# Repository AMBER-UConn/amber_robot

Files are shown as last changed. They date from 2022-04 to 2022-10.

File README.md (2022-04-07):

# The UConn AMBER (Adaptive Morphing and Balanced Exploratory Rover) Project

A group of students at the University of Connecticut were selected as finalists in the annual NASA Big Idea Challenge ([see our submission](https://bigidea.nianet.org/wp-content/uploads/2022-BIG-Idea-Challenge-Finalist-Team-Synopses.pdf) or the [video](https://youtu.be/4zF1PQumCn8))

# Project Setup
1. Download Git - [Linux](https://git-scm.com/download/linux), [macOS](https://git-scm.com/download/mac), [Windows](https://git-scm.com/download/win)
2. Download and Setup Docker
   - [macOS](https://docs.docker.com/desktop/mac/install/) - Install Docker Desktop
   - [Windows](https://docs.docker.com/desktop/windows/install/) - Install Docker Desktop
   - [Linux](https://docs.docker.com/engine/install/)
 #### On the terminal or command prompt do the following:
3. Navigate to a directory where you want the project to be stored.
4. Clone the GitHub Repository using the command - 
```
git clone https://github.com/AMBER-UConn/amber_robot
```
5. The docker configuration files lie in the docker folder of the amber_robot project. Anytime you need to access these files to run a command, change your current directory to the docker directory.
6. Before creating and starting any docker services, you must start Docker Daemon. In Windows or macOS, you can manually do it by starting the Docker Desktop app. The state should transition to "Running" after a few seconds. In Linux you can do it [manually](https://docs.docker.com/config/daemon/systemd/) or [automatically](https://docs.docker.com/engine/install/linux-postinstall/).
7. Return to the terminal and use the command below to create and start services.
```
docker-compose --profile no-gui up
``` 

8. After a while of downloading and compiling your containers will be up and running. You should see messages sent across ROS Services:
   
```
ros_listener  | data: "yoooooooooooooooooooooooooo 1"
ros_listener  | ---
ros_listener  | data: "yoooooooooooooooooooooooooo 2"
ros_listener  | ---
ros_listener  | data: "yoooooooooooooooooooooooooo 3"
ros_listener  | ---
```

   ## Congratulations! Set up complete!
\
   Note: To stop a running container, it would be preferable if the process could shutdown smoothly instead of abruptly disconnecting users and corrupting files. Press ctrl+c and wait 10-12 seconds for the containers to stop.

   Note: To restart the containers use the command `docker-compose up`.
   
\
To open a bash terminal (Linux terminal) in the rust_ros container, start the containers using the command `docker-compose up` in one tab of the terminal, and in another tab, start a bash terminal using the command:
 ```
 docker exec -it rust_ros bash
 ```

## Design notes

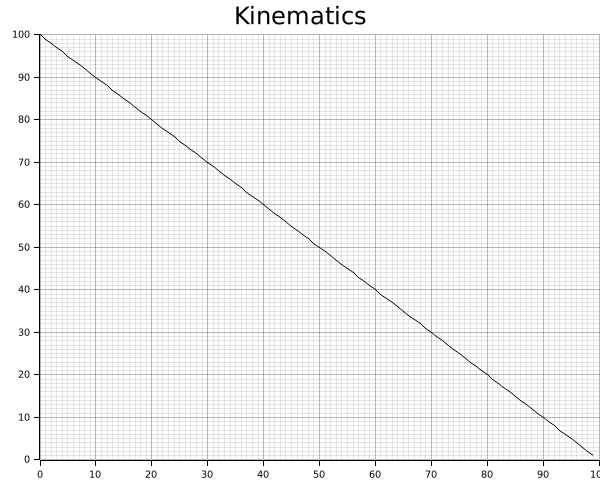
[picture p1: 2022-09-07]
rust-client/kinematics/curve.png

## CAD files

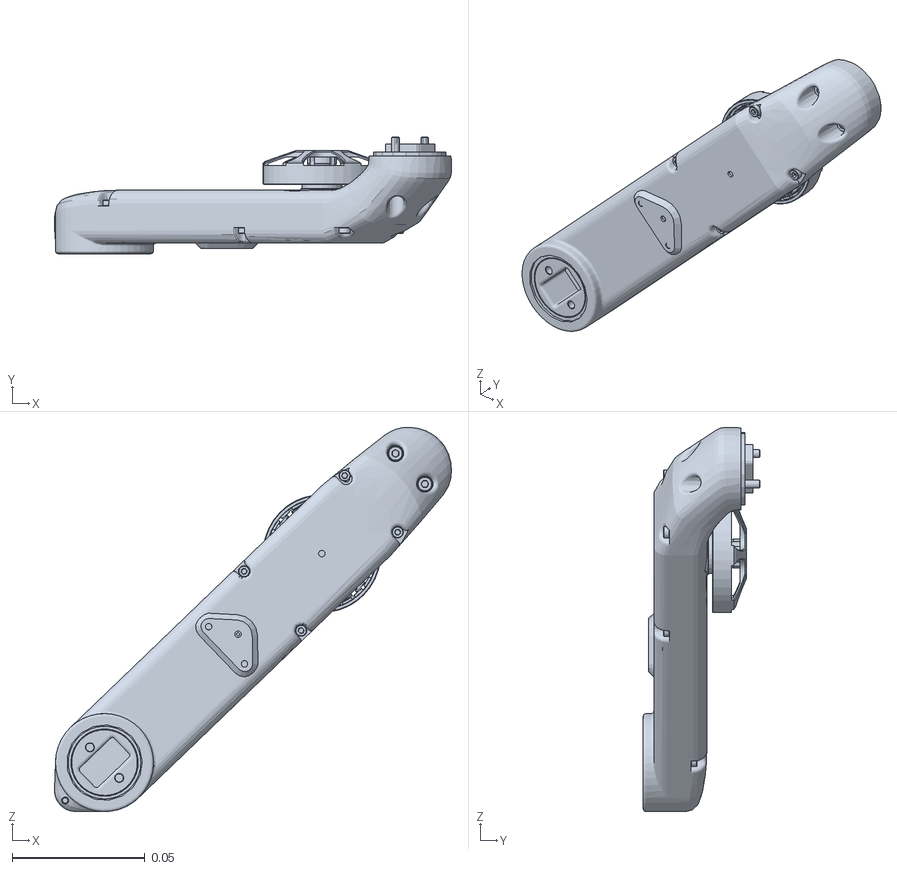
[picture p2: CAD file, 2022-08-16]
cw/src/2dof_leg_module_v3/meshes/upper_leg.STL
0.15 x 0.044 x 0.145

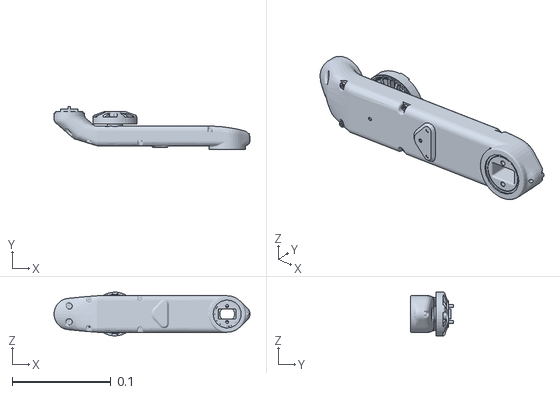
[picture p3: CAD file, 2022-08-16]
cw/src/2dof_leg_module_v3/meshes/hip_module.STL
0.199 x 0.044 x 0.0444

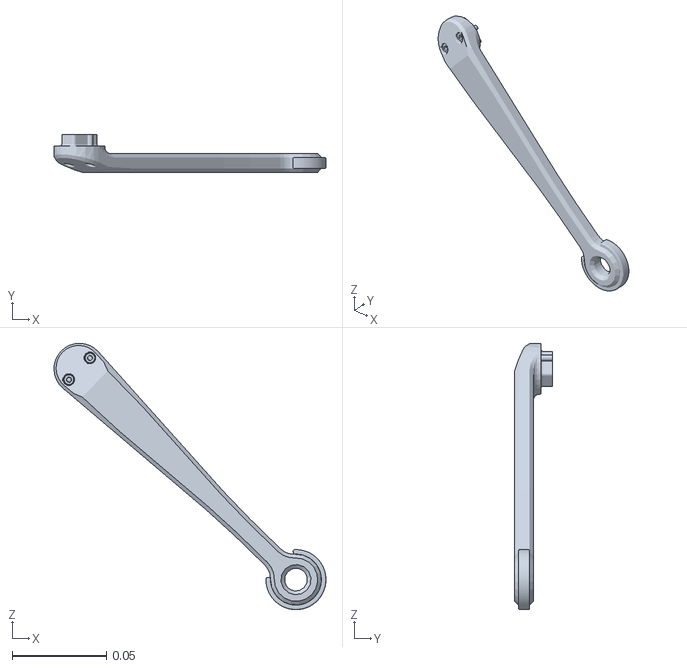
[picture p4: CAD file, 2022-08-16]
cw/src/2dof_leg_module_v3/meshes/lower_leg.STL
0.144 x 0.02 x 0.141

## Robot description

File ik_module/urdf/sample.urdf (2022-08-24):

<robot name="robo">
    <mujoco>
        <compiler meshdir="../meshes/" balanceinertia="true" discardvisual="false"/>
      </mujoco>
    <!-- links -->
    <link name="root_body">
      <inertial>
        <origin xyz="0 0 0.5" rpy="0 0 0"/>
        <mass value="1"/>
        <inertia ixx="100" ixy="0" ixz="0" iyy="100" iyz="0" izz="100" />
      </inertial>
      <visual>
        <origin xyz="0.0 0.0 0.0" rpy="0.0 0.0 0.0" />
        <geometry>
          <box size="0.2 0.2 0.4" />
        </geometry>
        <material name="Cyan">
          <color rgba="1.0 1.0 1.0 1.0"/>
        </material>
      </visual>
      <collision>
        <origin xyz="0 0 0" rpy="0 0 0"/>
        <geometry>
          <cylinder radius="1" length="0.5"/>
        </geometry>
      </collision>
    </link>
  
    <!-- left arm -->
    <link name="l_shoulder1">
      <visual>
        <origin xyz="0.0 0.0 0.0" rpy="0.0 0.0 0.0" />
        <geometry>
          <box size="0.1 0.1 0.1" />
        </geometry>
        <material name="Cyan">
          <color rgba="0 1.0 1.0 1.0"/>
        </material>
      </visual>
    </link>
    <link name="l_shoulder2">
      <visual>
        <origin xyz="0.0 0.0 0.0" rpy="0.0 0.0 0.0" />
        <geometry>
          <box size="0.1 0.1 0.1" />
        </geometry>
        <material name="Cyan">
          <color rgba="1.0 1.0 0.0 1.0"/>
        </material>
      </visual>
    </link>
    <link name="l_shoulder3">
      <visual>
        <origin xyz="0.0 0.0 0.0" rpy="0.0 0.0 0.0" />
        <geometry>
          <box size="0.1 0.1 0.2" />
        </geometry>
        <material name="Cyan">
          <color rgba="0.5 0.5 0.2 1.0"/>
        </material>
      </visual>
    </link>
    <link name="l_elbow1">
      <visual>
        <origin xyz="0.0 0.0 0.0" rpy="0.0 0.0 0.0" />
        <geometry>
          <box size="0.1 0.1 0.2" />
        </geometry>
        <material name="Cyan">
          <color rgba="0.8 0.2 0.2 1.0"/>
        </material>
      </visual>
    </link>
    <link name="l_wrist1">
      <visual>
        <origin xyz="0.0 0.0 0.0" rpy="0.0 0.0 0.0" />
        <geometry>
          <box size="0.1 0.15 0.1" />
        </geometry>
        <material name="Cyan">
          <color rgba="1.0 0.0 0.0 1.0"/>
        </material>
      </visual>
    </link>
    <link name="l_wrist2">
      <visual>
        <origin xyz="0.0 0.0 0.0" rpy="0.0 0.0 0.0" />
        <geometry>
          <box size="0.05 0.08 0.15" />
        </geometry>
        <material name="Cyan">
          <color rgba="0.0 0.0 1.0 1.0"/>
        </material>
      </visual>
    </link>
  
    <!-- right arm -->
    <link name="r_shoulder1">
      <visual>
        <origin xyz="0.0 0.0 0.0" rpy="0.0 0.0 0.0" />
        <geometry>
          <box size="0.1 0.1 0.1" />
        </geometry>
        <material name="Cyan">
          <color rgba="0 1.0 1.0 1.0"/>
        </material>
      </visual>
    </link>
    <link name="r_shoulder2">
      <visual>
        <origin xyz="0.0 0.0 0.0" rpy="0.0 0.0 0.0" />
        <geometry>
          <box size="0.1 0.1 0.1" />
        </geometry>
        <material name="Cyan">
          <color rgba="1.0 1.0 0.0 1.0"/>
        </material>
      </visual>
    </link>
    <link name="r_shoulder3">
      <visual>
        <origin xyz="0.0 0.0 0.0" rpy="0.0 0.0 0.0" />
        <geometry>
          <box size="0.1 0.1 0.2" />
        </geometry>
        <material name="Cyan">
          <color rgba="0.5 0.5 0.2 1.0"/>
        </material>
      </visual>
    </link>
    <link name="r_elbow1">
      <visual>
        <origin xyz="0.0 0.0 0.0" rpy="0.0 0.0 0.0" />
        <geometry>
          <box size="0.1 0.1 0.2" />
        </geometry>
        <material name="Cyan">
          <color rgba="0.8 0.2 0.2 1.0"/>
        </material>
      </visual>
    </link>
    <link name="r_wrist1">
      <visual>
        <origin xyz="0.0 0.0 0.0" rpy="0.0 0.0 0.0" />
        <geometry>
          <box size="0.1 0.15 0.1" />
        </geometry>
        <material name="Cyan">
          <color rgba="1.0 0.0 0.0 1.0"/>
        </material>
      </visual>
    </link>
    <link name="r_wrist2">
      <visual>
        <origin xyz="0.0 0.0 0.0" rpy="0.0 0.0 0.0" />
        <geometry>
          <box size="0.05 0.08 0.15" />
        </geometry>
        <material name="Cyan">
          <color rgba="0.0 0.0 1.0 1.0"/>
        </material>
      </visual>
    </link>
  
  

    <joint name="l_shoulder_yaw" type="revolute">
      <origin xyz="0.0 0.2 0.2" />
      <parent link="root" />
      <child link="l_shoulder1" />
      <axis xyz="0 0 1" />
      <limit lower="-3" upper="3.0" effort="0" velocity="1.0"/>
    </joint>
    <joint name="l_shoulder_pitch" type="revolute">
      <origin xyz="0.0 0.1 0.0" />
      <parent link="l_shoulder1" />
      <child link="l_shoulder2" />
      <axis xyz="0 1 0" />
      <limit lower="-3" upper="3.0" effort="0" velocity="1.0"/>
    </joint>
    <joint name="l_shoulder_roll" type="revolute">
      <origin xyz="0.0 0.1 0.0" />
      <parent link="l_shoulder2" />
      <child link="l_shoulder3" />
      <axis xyz="1 0 0" />
      <limit lower="-2" upper="3.0" effort="0" velocity="1.0"/>
    </joint>
    <joint name="l_elbow_pitch" type="revolute">
      <origin xyz="0.0 0.0 -0.2" />
      <parent link="l_shoulder3" />
      <child link="l_elbow1" />
      <axis xyz="0 1 0" />
      <limit lower="-2" upper="3.0" effort="0" velocity="1.0"/>
    </joint>
    <joint name="l_wrist_yaw" type="revolute">
      <origin xyz="0.0 0.0 -0.2" />
      <parent link="l_elbow1" />
      <child link="l_wrist1" />
      <axis xyz="0 0 1" />
      <limit lower="-2" upper="3.0" effort="0" velocity="1.0"/>
    </joint>
    <joint name="l_wrist_pitch" type="revolute">
      <origin xyz="0.0 0.0 -0.2" />
      <parent link="l_wrist1" />
      <child link="l_wrist2" />
      <axis xyz="0 1 0" />
      <limit lower="-2" upper="3.0" effort="0" velocity="1.0"/>
    </joint>
  
    <!-- right arm -->
    <joint name="r_shoulder_yaw" type="revolute">
      <origin xyz="0.0 -0.2 0.2" />
      <parent link="root" />
      <child link="r_shoulder1" />
      <axis xyz="0 0 1" />
      <limit lower="-3" upper="3.0" effort="0" velocity="1.0"/>
    </joint>
    <joint name="r_shoulder_pitch" type="revolute">
      <origin xyz="0.0 -0.1 0.0" />
      <parent link="r_shoulder1" />
      <child link="r_shoulder2" />
      <axis xyz="0 1 0" />
      <limit lower="-3" upper="3.0" effort="0" velocity="1.0"/>
    </joint>
    <joint name="r_shoulder_roll" type="revolute">
      <origin xyz="0.0 -0.1 0.0" />
      <parent link="r_shoulder2" />
      <child link="r_shoulder3" />
      <axis xyz="1 0 0" />
      <limit lower="-2" upper="3.0" effort="0" velocity="1.0"/>
    </joint>
    <joint name="r_elbow_pitch" type="revolute">
      <origin xyz="0.0 0.0 -0.2" />
      <parent link="r_shoulder3" />
      <child link="r_elbow1" />
      <axis xyz="0 1 0" />
      <limit lower="-2" upper="3.0" effort="0" velocity="1.0"/>
    </joint>
    <joint name="r_wrist_yaw" type="revolute">
      <origin xyz="0.0 0.0 -0.2" />
      <parent link="r_elbow1" />
      <child link="r_wrist1" />
      <axis xyz="0 0 1" />
      <limit lower="-2" upper="1.0" effort="0" velocity="1.0"/>
    </joint>
    <joint name="r_wrist_pitch" type="revolute">
      <origin xyz="0.0 0.0 -0.2" />
      <parent link="r_wrist1" />
      <child link="r_wrist2" />
      <axis xyz="0 1 0" />
      <limit lower="-2" upper="3.0" effort="0" velocity="1.0"/>
    </joint>
  </robot>

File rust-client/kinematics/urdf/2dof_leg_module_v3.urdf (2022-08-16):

<?xml version="1.0" encoding="utf-8"?>
<!-- This URDF was automatically created by SolidWorks to URDF Exporter! Originally created by Stephen Brawner (brawner@gmail.com) 
     Commit Version: 1.6.0-4-g7f85cfe  Build Version: 1.6.7995.38578
     For more information, please see http://wiki.ros.org/sw_urdf_exporter -->
<robot name="2dof_leg_module_v3">
  <mujoco>
    <compiler meshdir="../meshes/" balanceinertia="true" discardvisual="false"/>
  </mujoco>
  <link name="hip_module">
    <inertial>
      <origin xyz="-0.0135872417794477 0.00419665468565325 -0.0185249720276986" rpy="0 0 0" />
      <mass value="0.0938334172894058" />
      <inertia ixx="1.46634528569586E-05" ixy="1.02326144382057E-05" ixz="-7.7018336582582E-08" iyy="0.000157483495316331" iyz="6.78740712115125E-09" izz="0.000152202454585631" />
    </inertial>
    <visual>
      <origin xyz="0 0 0" rpy="0 0 0" />
      <geometry>
        <mesh filename="package://2dof_leg_module_v3/meshes/hip_module.STL" />
      </geometry>
      <material name="">
        <color rgba="0.752941176470588 0.752941176470588 0.752941176470588 1" />
      </material>
    </visual>
    <collision>
      <origin xyz="0 0 0" rpy="0 0 0" />
      <geometry>
        <mesh filename="package://2dof_leg_module_v3/meshes/hip_module.STL" />
      </geometry>
    </collision>
  </link>
  <link name="upper_leg">
    <inertial>
      <origin xyz="-0.0578208195636141 -0.0212739250328726 -0.0555577921645933" rpy="0 0 0" />
      <mass value="0.094277083667373" />
      <inertia ixx="8.19279303589027E-05" ixy="-7.26529131974399E-06" ixz="-6.98506331572851E-05" iyy="0.000159785167856354" iyz="-6.99467251943385E-06" izz="8.72625226077833E-05" />
    </inertial>
    <visual>
      <origin xyz="0 0 0" rpy="0 0 0" />
      <geometry>
        <mesh filename="package://2dof_leg_module_v3/meshes/upper_leg.STL" />
      </geometry>
      <material name="">
        <color rgba="0.752941176470588 0.752941176470588 0.752941176470588 1" />
      </material>
    </visual>
    <collision>
      <origin xyz="0 0 0" rpy="0 0 0" />
      <geometry>
        <mesh filename="package://2dof_leg_module_v3/meshes/upper_leg.STL" />
      </geometry>
    </collision>
  </link>
  <joint name="hip_joint" type="continuous">
    <origin xyz="0.066577 -0.011968 -0.0185" rpy="0 0 0" />
    <parent link="hip_module" />
    <child link="upper_leg" />
    <axis xyz="0 1 0" />
  </joint>
  <link name="lower_leg">
    <inertial>
      <origin xyz="0.047875486284217 -0.0138955733287597 -0.0466193127886608" rpy="0 0 0" />
      <mass value="0.0374009758334682" />
      <inertia ixx="5.04189375716838E-05" ixy="1.3994879750165E-06" ixz="4.99489822029058E-05" iyy="0.000102550238222013" iyz="-1.36276953731254E-06" izz="5.30753304664563E-05" />
    </inertial>
    <visual>
      <origin xyz="0 0 0" rpy="0 0 0" />
      <geometry>
        <mesh filename="package://2dof_leg_module_v3/meshes/lower_leg.STL" />
      </geometry>
      <material name="">
        <color rgba="0.752941176470588 0.752941176470588 0.752941176470588 1" />
      </material>
    </visual>
    <collision>
      <origin xyz="0 0 0" rpy="0 0 0" />
      <geometry>
        <mesh filename="package://2dof_leg_module_v3/meshes/lower_leg.STL" />
      </geometry>
    </collision>
  </link>
  <joint name="knee_joint" type="continuous">
    <origin xyz="-0.11534 -0.0324 -0.11089" rpy="0 0 0" />
    <parent link="upper_leg" />
    <child link="lower_leg" />
    <axis xyz="0 1 0" />
  </joint>
</robot>

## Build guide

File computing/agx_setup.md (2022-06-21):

# Configuring CAN on the AGX
See [this article](https://medium.com/@ramin.nabati/enabling-can-on-nvidia-jetson-xavier-developer-kit-aaaa3c4d99c9) for a more detailed overview
1. Install `busybox` to change register values
```sudo apt install busybox```

2. The can_setup.sh script should run at the start but if not, you can run it manually

*Note* the pinout of the AGX fallows the Raspi 40 pin standard normally but the following pin configurations are changed
_Pin | Type_
37/29 | CAN RX
33/31 | CAN TX
34/30 | Ground
17/1  | 3.3V

## How to start `can_setup.sh` on startup
1. Create a symlink for the can_setup.sh script onto the root directory
`ln -s ~/amber_robot/computing/can_setup.sh /`
2. Run the enable_can_setup.sh script which should automatically configure the script to run on startup

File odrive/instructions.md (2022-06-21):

To start the odrive make sure that 
1. All the motor phase wires are plugged in
2. The power supply is plugged into an outlet
3. The odrive is connected to the AGX via USB

To start an interactive session with the odrive, run `odrivetool` in the terminal

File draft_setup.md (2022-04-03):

# General information
There are several main components interacting in this project. We will be building our design off the ROS framework () which is language agnostic (can use anything). Which is the reason why we are building our project off of Rust!

### Why Rust? ###

**A few main benefits:**
- Statically typed (unlike Python)
- Memory safety out of the box (no null pointers, dangling references)
- Thread safety out of the box
- Package management (which is non-existent with C++)

However, there are also a few pratical reasons outside the tech specs of the language. We have to face the reality that we do not know everything. We are not well versed in the intricacies of the frameworks, programming languages, and even the concepts we are trying to implement. And it may seem counter-intuitive that having everyone learn a whole new language is time efficient, but in reality we are saving ourselves from a world of pain by using Rust (over the alternative of C++). We would like to increase our chances of bowling a perfect 300, and Rust is basically the gutterball guard rail preventing us from messing up. 

I do concede that the documentation is less available for Rust based ROS projects, however there is enough to build off of for our purpose. We are going to build off of the package `rosrust` (which is just a Rust client implementation for ROS).

However I highly recommend that we take inspiration from the `openrr` on how to architecture our code since it has many many functions that we need for our purposes already implemented. Unfortunately, after some testing, not all of the code compiles so we can't build off of it directly (not to mention a lack of documentation).

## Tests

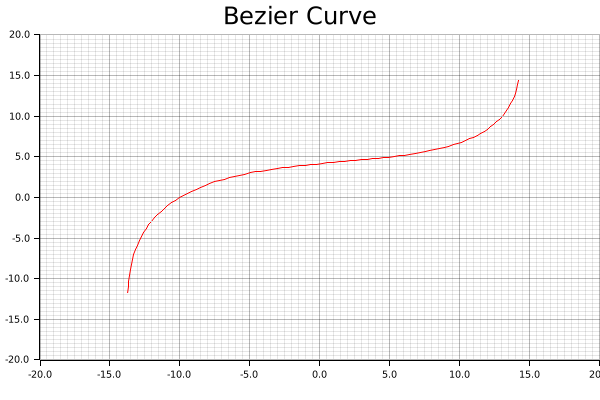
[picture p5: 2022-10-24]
rust-client/kinematics/test.png

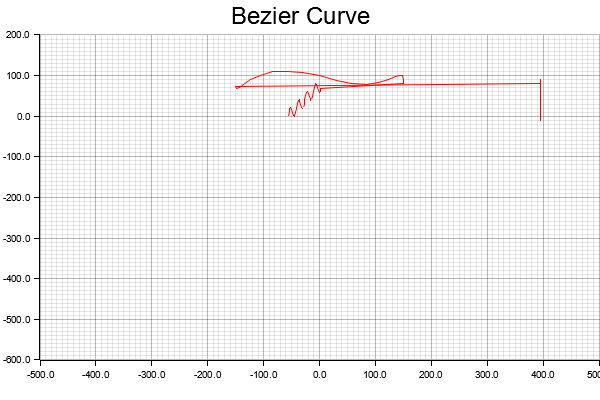
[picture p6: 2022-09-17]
rust-client/kinematics/src/test.png

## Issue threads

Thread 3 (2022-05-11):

Configure odrives with the motors, jetson, power supply, and odrives

kalinkochnev, 2022-05-11:

kalinkochnev, 2022-07-01:
Single power supply and odrive have been wired and functional for quite some time. Now we are focusing on finding the proper batteries and avoiding ground loops

Closed 2022-07-01.

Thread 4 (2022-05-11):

Create sketch (and CAD drawing) for leg test stand V1

kalinkochnev, 2022-05-11:
We need to build a leg test stand, preferably before the mid project report or have made big strides towards building one. We will have some spare wood to work with from the MSL, as well as 3D printers and the likes of that. Try to avoid building this with any parts we do not have easily accessible. Reference our stock sheet for what we have available.

**Build requirements:**
1. Have a stable foundation that can avoid shaking too much and can be clamped down
2. Be tall enough the have the leg fully extended vertically and not be touching the surface the stand is on, plus add an 2 inches of extra height so that we may be able to put things below the leg without issue.
3.  Have a place to mount an ODrive and a power supply (where the odrive and power supply should be able to be removed). _Suggestions_: 3d print mounting brackets so things can slide in and out.

4. Have cables be routed to avoid getting tangled up in the leg (also may want to 3d print cable brackets of some kind)
5. Be able to screw the leg into the beam somehow

Message Kalin to measure dimensions of parts when he's in the lab (e.g. power supply, wood beams, odrive, etc)

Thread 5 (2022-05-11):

2 DOF Leg simulation in Gazebo

kalinkochnev, 2022-05-11:
Use gazebo to simulate a fixed base, 2 degree of freedom leg.

**Requirements**
1. Make a rudimentary URDF model of a 2 DOF leg (someone else will be tasked with creating a more accurate one)
2. Control the simulated leg through the rosrust client (just needs to move somehow, could spin in circles for all I care)
3. Figure out how to actually control the simulated leg well. We are effectively building a robot arm, so I'm sure there are a lot of tutorials on how to do inverse kinematics.

**Suggestions**
- look into the ROS package called ros_control for motor control (which is pretty popular and should maybe be able to integrate with gazebo. This is what the odrive motor controller package is build off of, so it should be swappable)
- Try using the `ikfast` library http://wiki.ros.org/Industrial/Tutorials/Create_a_Fast_IK_Solution, http://openrave.org/docs/latest_stable/openravepy/ikfast/#ik-types

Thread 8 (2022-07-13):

OPAMP_DISABLED

UltraArceus3, 2022-07-13:
Seemingly at random, the motors would refuse to beep and turn during full calibration sequence. Instead, the motor would either twitch in-place or do nothing at all. This would seemingly come in and out at inconvenient times.
Checking the motor for errors would reveal a 'MotorError.OPAMP_DISABLED' error. There are no documentations nor resources from ODrive discussing the error, the cause of the error, or a solution. Asking on the ODrive forums or Discord has shown that no one knows what the error is nor the cause of it.

UltraArceus3, 2022-07-13:
Some temporary solutions I've found while testing:
- Unplugging and plugging in the ODrive
- Swapping the motors between axes / ODrives
- Tilting the motor at an angle or placing it upside-down
- Slightly bending the motor's cable
- Repeatedly sending the Full Calibration Sequence command

I have not tested these enough to know if they truly work as this error does come and go randomly, so some of these may be false positives.

UltraArceus3, 2022-07-14:
https://discourse.odriverobotics.com/t/op-amp-error-odrive/9443

UltraArceus3, 2022-07-14:
According to the forum post, OPAMP_DISABLED is an outdated error w/ its corresponding value being reassigned to UNBALANCED_PHASES.
Upon further research, UNBALANCED_PHASES may be remedied by using thicker gauge wires.

UltraArceus3, 2022-07-14:
Swapping the 26AWG motor cables with 22AWG seems to have remedied the error from all the motors.

Further testing is needed, but the issue seems to have disappeared. I'll reopen this if the error comes up again.

Closed 2022-07-14.

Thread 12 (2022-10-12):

Controlling tank tread motors via RP4

kalinkochnev, 2022-10-12:
**Task:**
make an API for CAN communication from the Arduino to the RP4 for tread motor control

**Tread control requirements:**
- Individually addressable motors
- Set parameters such as velocity, direction

**Implementation:**
- Raspberry Pi sends commands across CAN
- Rust client maintains current state of tread control, commands sent update internal state as well, returns a result
- Arduino processes incoming messages across CAN
- Arduino responds with OK message if successful, Err if not

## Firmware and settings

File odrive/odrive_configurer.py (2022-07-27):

"""This files should be run to either reset or setup an odrive that uses 2 Antigravity motors

https://store.tmotor.com/goods.php?id=438
https://docs.odriverobotics.com/v/latest/getting-started.html

Before running the script, make sure you activate `odrivetool` and then
add this python package to the list of modules at runtime 

```
import sys
sys.path.insert(1, "/home/nvidia/amber_robot/odrive") # 0 is the odrivetool script path, 1 is the place we want to put our package

import setup
setup.setup_axes(odrv0, [odrv0.axis0, odrv0.axis1])
```
"""

#from tkinter import S
from typing import List
from odrive.enums import *
import odrive
from fibre.libfibre import ObjectLostError
import time
import sys
import init_motors


class RoverMotorConfig:
    """
    Class for configuring an Odrive axis for a Amber motor. 
    Only works with one Odrive at a time.
    """
    ########
    MOTOR_KV = 300
    ENCODER_CPR = 8192  # counts per revolution for the AMT - 102 Encoder
    NUM_POLES = 24
    VBUS_VOLTAGE = 24
    CAN_BAUD_RATE = 250000


    def __init__(self, axis_num, odrv, sensorless = False, _output = True, _force_sensorless = True):
        """
        Initalizes RoverMotorConfig class by finding odrive, erase its 
        configuration, and grabbing specified axis object.

        :param axis_num: Which channel/motor on the odrive your referring to.
        :type axis_num: int (0 or 1)
        """
        self.axis_num = axis_num
        self.axis = None
        self.odrv = odrv
        self.sensorless = sensorless
        self._force_sensorless = _force_sensorless

        self.output = _output
        # Connect to Odrive

        self.axis = self.get_axis(self.axis_num, self.odrv)

    @classmethod
    def get_odrive(cls, output = False):
        # connect to Odrive
        print("Looking for ODrive...") if output else None
        odrv = odrive.find_any()
        print("Found ODrive.") if output else None
        return odrv

    @classmethod
    def get_axis(cls, axis_num, odrv):
        return getattr(odrv, f"axis{axis_num}")

    @classmethod
    def config_power_supply(cls, odrv):
        #  power configuration for AC/DC Power Supply
        odrv.config.dc_bus_overvoltage_trip_level = 25
        odrv.config.dc_max_positive_current = 10
        odrv.config.dc_max_negative_current = -1

    @classmethod
    def config_lipo_battery(cls, odrv):
        print("Please enter battery ratings as asked.")
        batt_n_cells = int(input("Enter number of cells in series: "))
        batt_capacity = int(input("Enter battery capacity in mAh: ")) / 1000
        odrv.config.dc_bus_undervoltage_trip_level = 3.25 * batt_n_cells
        odrv.config.dc_bus_overvoltage_trip_level = 4.25 * batt_n_cells
        #self.odrv.config.dc_max_positive_current = batt_capacity * 50
        #self.odrv.config.dc_max_negative_current = -batt_capacity * 1 # CHECK THIS CAREFULLY

    def configure(self, CAN_id):
        # This is to lower the amount of power going back into the odrive when the motor is braking
        self.odrv.config.enable_brake_resistor = True

        

        self.config_motors()
        self.config_sensorless() if self.sensorless else self.config_encoder()
        self.config_CAN(CAN_id)

        self.axis.controller.config.control_mode = CONTROL_MODE_VELOCITY_CONTROL
        self.axis.controller.config.vel_limit = 50

        self.odrv.config.brake_resistance = 1
        self.axis.controller.config.input_mode = INPUT_MODE_VEL_RAMP
        

        return self.odrv

    
    def config_motors(self):
        # The motors have a peak current of 9 amps
        self.axis.motor.config.current_lim = 9
        self.axis.motor.config.requested_current_range = 10

        # The speed of the motor will be limited to this speed in [turns/sec]
        self.axis.controller.config.vel_limit = 50
        self.axis.motor.config.pole_pairs = RoverMotorConfig.NUM_POLES / 2 # The MN4004 has 24 magnet poles, so 12 pole pairs
        # The MN4004 has an idle current of 0.2 A but we set it at 2 for it to go faster during calibration
        self.axis.motor.config.calibration_current = 2
        
        self.axis.config.calibration_lockin.current = 2
        # to avoid motors from heating up when finding index (ENCODER_INDEX_SEARCH)
        
        # this is specified in the odrive documentation
        self.axis.motor.config.torque_constant = 8.27 / RoverMotorConfig.MOTOR_KV
        # self.axis.motor.config.resistance_calib_max_voltage = 0.4 * VBUS_VOLTAGE ****do not use

        self.axis.motor.config.motor_type = MOTOR_TYPE_HIGH_CURRENT

    def config_encoder(self):
        if self.axis.config.enable_sensorless_mode: return

        self.axis.controller.config.vel_gain = 0.01
        self.axis.controller.config.pos_gain = 212.0

        #vel_integrator_gain = 0.5 * vel_gain * bandwidth (in hertz)
        self.axis.controller.config.vel_integrator_gain = 0.5 * self.axis.controller.config.vel_gain * 1/(self.axis.encoder.config.bandwidth/1000)

        self.axis.encoder.config.cpr = RoverMotorConfig.ENCODER_CPR
        #self.axis.encoder.config.mode = ENCODER_MODE_INCREMENTAL
        self.axis.encoder.config.use_index = True

    def config_sensorless(self):
        self.axis.config.enable_sensorless_mode = True

        self.axis.controller.config.vel_gain = 0.01
        self.axis.controller.config.vel_integrator_gain = 0.05

        # 5 turns_per_sec / (2 * 3.14159265 * NUM_POLES / 2)
        self.axis.sensorless_estimator.config.pm_flux_linkage = 5.51328895422 / (2 * RoverMotorConfig.NUM_POLES * RoverMotorConfig.MOTOR_KV)

    def config_CAN(self, can_axis_id):
        self.odrv.can.config.baud_rate = RoverMotorConfig.CAN_BAUD_RATE
        self.axis.config.can.node_id = can_axis_id

    def check_error(self, obj):
        if hasattr(obj, "error"):
            if obj.error != 0:
                print("\nERROR \n"
                      "ODrive reported error {}.\n"
                      "Dumping object data:\n{}\n".format(obj.error, obj))
                return False
        return True

    def motor_calib(self):
        print("\nCalibrating Motor {} (You should hear a beep)...".format(self.axis_num))
        self.axis.requested_state = AXIS_STATE_MOTOR_CALIBRATION

        # Wait for calibration to take place
        wait_until(lambda : self.axis.motor.config.phase_inductance != 0)
        print("phase inductance: {}".format(self.axis.motor.config.phase_inductance))

        if self.check_error(self.axis.motor):
            self.axis.motor.config.pre_calibrated = True


    def encoder_calib(self, use_index=True, sensorless_enc_error = True):
        #Skips Encoder Calibration if Motor Calibration failed
        if not(self.axis.motor.config.pre_calibrated):
            return

        if use_index:
            self.axis.encoder.config.use_index = True
            print("Rotating Encoder {} back to index...".format(self.axis_num))
            self.axis.requested_state = AXIS_STATE_ENCODER_INDEX_SEARCH
            time.sleep(3)


        print("Calibrating Encoder {} (The motor should rotate back-and-forth)...".format(self.axis_num))
        self.axis.requested_state = AXIS_STATE_ENCODER_OFFSET_CALIBRATION
        #waits until encoder finishes calibrating or throws an error
        wait_until(
            lambda :
            (abs(self.axis.encoder.config.direction) == 1 and
            self.axis.encoder.config.phase_offset != 0) or
            self.axis.encoder.error != 0
            )

        if self.check_error(self.axis.encoder):
            self.axis.encoder.config.pre_calibrated = True
        elif sensorless_enc_error:
            print("Encoder Error")
            if self._force_sensorless:
                print("Reverting to sensorless mode...")
                self.sensorless = True
                self.config_sensorless()
            #If there is an encoder error (i.e. encoder isn't detected), the motor becomes sensorless
            

    def run_calib(self, odrv):
        self.odrv = odrv
        self.axis = self.get_axis(self.axis_num, self.odrv)
        self.motor_calib()
        self.encoder_calib() if not(self.sensorless) else None

def save(odrv = RoverMotorConfig.get_odrive()):
    try:
        odrv.save_configuration()
    except ObjectLostError:
        pass
    return RoverMotorConfig.get_odrive()

def wait_until(cond, sec_limit: float = 10.0):
    tick = 0
    while not(cond()) and tick < sec_limit:
        time.sleep(0.1)
        tick += 0.1
    print("wait timed out") if tick >= sec_limit else None

def main():
    odrv = RoverMotorConfig.get_odrive(True)
    print("Erasing pre-existing configuration...")
    try:
        odrv.erase_configuration()
    except:
        pass

    odrv = RoverMotorConfig.get_odrive()

    odrv_can_id = 2 * int(input("ODrive CAN ID > "))

    odrive_config1 = RoverMotorConfig(axis_num = 0, _force_sensorless = False, odrv = odrv)
    odrv = odrive_config1.configure(CAN_id = odrv_can_id)

    odrive_config2 = RoverMotorConfig(axis_num = 1, _force_sensorless = False, odrv = odrv)
    odrv = odrive_config2.configure(CAN_id = odrv_can_id + 1)


    power_supply_type = int(input("Enter 1 for Bench Power Supply or 2 for Battery > "))
    match power_supply_type:
        case 1:
            RoverMotorConfig.config_power_supply(odrv)
        case 2:
            RoverMotorConfig.config_lipo_battery(odrv)
        case _:
            raise ValueError("Incorrect Input!")

    odrv = save(odrv)
    
    input("Make sure the motor is free to move, then press enter...")

    odrive_config1.run_calib(odrv)
    odrive_config2.run_calib(odrv)

    print("Saving...")
    odrv = save(odrv)
    print("Calibration Complete!")
    return odrv


if __name__ == "__main__":
    o = main()

    print("Initializing Motors...")
    init_motors.init(o)

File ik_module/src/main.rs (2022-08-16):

use k::*;

fn main() {
    // // Load urdf file
    // let chain = k::Chain::<f32>::from_urdf_file("/home/vihaan/Projects/amber/amber_robot/ik_module/urdf/2dof_leg_module_v3.urdf").unwrap();
    // println!("chain: {chain}");
    // assert_eq!(chain.dof(), 2);

    // // // Set initial joint angles
    // // let angles = vec![0.2, 0.2, 0.0, -1.0, 0.0, 0.0, 0.2, 0.2, 0.0, -1.0, 0.0, 0.0];
    // let angles = vec![0.0, 0.0];
    // println!("angles: {:?}", angles);


    // chain.set_joint_positions(&angles).unwrap();
    // println!("initial angles={:?}", chain.joint_positions());

    // let target_link = chain.find("hip_joint").unwrap();

    // // Get the transform of the end of the manipulator (forward kinematics)
    // chain.update_transforms();
    // let mut target = target_link.world_transform().unwrap();

    // println!("initial target pos = {}", target.translation);
    // // println!("move z: +0.1");
    // // target.translation.vector.z += 0.1;

    // // Create IK solver with default settings
    // let solver = k::JacobianIkSolver::default();

    // // Create a set of joints from end joint
    // let arm = k::SerialChain::from_end(target_link);
    // println!("arm dof {}", arm.dof());

    // // solve and move the manipulator angles
    // solver.solve(&arm, &target).unwrap();
    // println!("solved angles={:?}", chain.joint_positions());

    // chain.update_transforms();
    // let solved_pose = target_link.world_transform().unwrap();
    // println!("solved target pos = {}", solved_pose.translation);




    use k::prelude::*;

    let chain = k::Chain::<f32>::from_urdf_file("/home/vihaan/Projects/amber/amber_robot/ik_module/urdf/2dof_leg_module_v3.urdf").unwrap();
    // Create sub-`Chain` to make it easy to use inverse kinematics
    let target_joint_name = "hip_joint";
    let r_wrist = chain.find(target_joint_name).unwrap();
    let mut arm = k::SerialChain::from_end(r_wrist);
    println!("arm: {arm}");

    // Set joint positions of `arm`
    let positions = vec![0.0];
    arm.set_joint_positions(&positions).unwrap();
    println!("initial positions={:?}", arm.joint_positions());

    // Get the transform of the end of the manipulator (forward kinematics)
    let mut target = arm.update_transforms().last().unwrap().clone();

    println!("initial target pos = {}", target.translation);
    println!("move x: -0.1");
    target.translation.vector.x -= 0.1;
    
    // Create IK solver with default settings
    let solver = k::JacobianIkSolver::default();

    let mut constraints = k::Constraints::default();
    constraints.rotation_x = false;
    constraints.rotation_z = false;
    constraints.position_x = false;
    constraints.position_y = false;
    constraints.position_z = false;

    solver
        .solve_with_constraints(&arm, &target, &constraints)
        .unwrap_or_else(|err| {
            println!("Err: {err}");
   });
    // solve and move the manipulator positions
    // solver.solve(&arm, &target).unwrap();


    println!("solved positions={:?}", arm.joint_positions());
}

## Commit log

2022-03-29 Added urdf-visualizer
    [test.urdf]
2022-03-30 Added basic setup instructions
    [test.urdf]
2022-04-03 Made progress towards running rust inside container
    [test.urdf]
2022-06-09 Succesfully created odrive configuration to spin motors
2022-06-10 Added instructions to start odrive
2022-06-17 ODrive CAN control demonstrated with test script
2022-06-20 Added ODrive CAN and AxisState constants.
2022-06-20 Outlined abstracted methods for ODrive CAN calls
2022-06-21 Odrive configuration was significantly improved. Calibration sequence does not run correctly
    [streamlined_odrive_config.py]
2022-06-21 CAN data successfully received by Odrive from Rust!
2022-06-21 Outlined CANManager, ODrive message and responses. Setup initialization of channels between threads
2022-06-22 "wired up" communication channels between CANMan and main thread
2022-06-22 Implemented CANThreadCommunicator for ODriveGroup and added default impl for send_to_manager
2022-06-22 Added function to register threads to the canproxy
2022-06-24 Added cansocket as module to lib and "mock-socket" feature
2022-06-24 Register and unregistering thread passes
2022-06-27 ODriveCANFrame is converted back and forth properly. All tests pass
2022-06-27 Added thread stub to be importable for testing in the package
2022-06-27 Added read-only and read-write thread register functions to prevent accessing the same resource as write twice
2022-06-27 Created default implementations for CANThreadCommunicator and switched to struct composition paradigm instead of traits
2022-06-29 Implemented messages sending/receiving on canproxy. Also allowed threads to exit peacefully (incomplete)
2022-06-30 Changed ODriveResponse to use normal Results instead of custom
2022-06-30 Test of can_proxy for real can socket. Need to improve stopping of threads
2022-06-30 disable mosocket for agx testing + successfully recieved / sent commands to odrives
2022-07-01 Benchmark of can_proxy with mock socket is functional
2022-07-01 Made begin() function for CANProxy return a handle to stop all threads
2022-07-06 Fixed odrive axis erasure bug.
    [odrive_configurer.py]
2022-07-07 Fixed Lost Object Error for ODrive + Axis
    [odrive_configurer.py]
2022-07-08 Added Raspberry Pi CAN HAT configuration script Co-authored-by: Rany Kamel <rany.kamel47@gmail.com>
2022-07-08 Rust CAN test code runs calibration on both motors
2022-07-08 Sends motor state signal to two CAN buses
2022-07-11 Implemented Axis set state for odrive group
2022-07-11 Individual Motor Testing w/ Multiple ODrives + Implemented ClosedLoop State
2022-07-12 Moved axis, motor, and encoder into separate file.
    Reordered structs in messages.rs
2022-07-12 Refactored ODriveResponse to use Results and ResponseType for more detailed requests and responses
    Introduced type alias CANRequest/CANResponse for ODriveCANFrame
2022-07-12 Added documentation for ODriveGroup
2022-07-19 Added encoder configuration
2022-07-19 Encoder Calib. ends if no encoder is detected + Motor becomes sensorless if no encoder is detected
2022-07-20 Started controller tuner script w/ basic ui + changed odrive_configurer to act as library for the tuner script
2022-07-21 Added send_command + CAN velocity testing
2022-07-22 CAN controls motor velocity
2022-07-25 Added Power Supply Config Settings
2022-07-25 Changed Power Supply Config
2022-07-25 Added Set Velocity and Set Position functions + implemented way to convert float to binary to send over CAN
2022-07-25 Renamed Enum Read and Write to ReadComm and WriteComm to avoid confusion with functions Read and Write
    [main.rs]
2022-07-25 Added reduced lockin current for heat issues + battery power supply
    [odrive_configurer.py]
2022-07-26 Changes to config PS/Battery
2022-07-26 Added basic GUI to control velocity and position
2022-07-26 Made forcing sensorless when encoder failed togglable + Fixed power functions + Encoder Cal. is skipped if Motor Cal. failed
    [odrive_configurer.py]
2022-07-26 Error thrown if neither PS or Battery is selected
    [odrive_configurer.py]
2022-07-26 Removed newline from input + script takes 6 motors
2022-07-27 Added motor initalization script
2022-07-27 Added motor initialization to CAN script
2022-07-28 Added ui command to manually initalize motors
2022-08-03 Fixed rustodrive using fake CAN socket
    [main.rs]
2022-08-16 added basic configuration
    [2dof_leg_module_v3.urdf, hip_module.STL, lower_leg.STL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]
2022-08-16 basic configuration
    [2dof_leg_module_v3.urdf, hip_module.STL, lower_leg.STL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]
2022-08-16 changed axes orientation
    [2dof_leg_module_v3.urdf]
2022-08-23 added trig method for forward kinematics
2022-08-24 added urdf and urdf-parser
    [2dof_leg_module_v3.urdf, sample.urdf]
2022-08-25 added partial analytical inverse kinematics solution
    [sample.urdf]
2022-09-04 added correct generic return type
    [main.rs]
2022-09-05 restructed and renamed folders and files
    [2dof_leg_module_v3.urdf]
2022-09-09 Added de casteljau's alg
2022-09-09 Fixed up decasteljau's alg and added test code
    [main.rs]
2022-09-10 Fixed type specifications for plotting library and imports
    [main.rs]
2022-09-17 Added eqs from single leg paper
2022-10-09 removed duplicate inverse kinematics directory
    [2dof_leg_module_v3.urdf]
2022-10-14 moved kinematics directory into rust-client directory
    [2dof_leg_module_v3.csv, 2dof_leg_module_v3.urdf, hip_module.STL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]
2022-10-15 rectified cubic bezier curve eqn and implemented it with inverse kinematics
2022-10-23 deleted urdf_parser
2022-10-24 added some print statements for debugging
2022-10-24 fixed inverse_ik theta2 bug
    [main.rs]
